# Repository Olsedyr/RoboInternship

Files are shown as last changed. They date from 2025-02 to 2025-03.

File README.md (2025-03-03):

# RoboInternship
The github repo for RoboStacker/MPN internship

CompanyDocumentation indeholder dokumentation for firmaets opbygning og kode. 

Brugen af el-dokumenter:

Åben CaddyDFX filerne i et program der understøtter .dfx filtyper, såsom LibreCAD (Open Source)

DFXComponentsLibrary består af komponenter i .dfx formatet. 

Eksempel til implementering a DFXComponentsLibrary i LibreCAD:

	1. Åben LibreCad
	2. Klik på 'options' 
	3. Vælg 'Apllication Preferences' 
	4. Gå til 'Paths'	
	5. Indsæt stien til DFXComponentsLibrary fra GitHub-repo klonen i 'part libraries' feltet. 
	6. Genstart libreCAD

 For at tilføje flere komponenter skal mappen med de nye komponenter i filformatet .dfx indsættet i DFXComponentsLibrary-mappen.

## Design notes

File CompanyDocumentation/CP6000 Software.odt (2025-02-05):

CP6000 v2007 software

Preliminary Technical Manual

# Statemashines

## Standard Statemachines

### 708WorkCell.statemachine

File containing other file names, which should be included in the workcell.

STATEMACHINEVERSION 3

Include=cpworkcell.statemachine

Link=PIDBuffer ServoBuffer

Link=PIDLift ServoLift

Link=PIDSkub ServoSkub

Link=extra1 AccumulatingConveyor

(Inlcude cpworkcell.statemachine below:)

STATEMACHINEVERSION 3

Name=WorkCell

Link=Emergency

Link=ContinueKnap

Link=ErrorCode

Link=BufferPlads

Link=KasseInLiner

Link=KasseLift

Link=LangBufferSkub

Link=PIDBuffer

Link=PIDLift

Link=PIDSkub

Link=ProductConveyors

Link=extra1 ProductConveyors

linkValue=newprogram Program

Value=errorCode 0

Value=firstRun 0

Value=doFakeProducts 0

Timeout=timeBeforeRunning 3000000

Timeout=timeBeforePausing 2000000

State=ST_HALT

END

State=ST_IDLE

SET errorCode 0

TEST ContinueKnap = ST_HIGH

TIMEOUT timeBeforeRunning ST_STARTING

SETSTATE ST_STARTING

ENDTEST

END

State=ST_STARTING

SET firstRun 1

TEST timeBeforeRunning = 1

SETSTATE ST_RUNNING

ENDTEST

TEST Emergency = ST_POWEROFF

SET errorCode 203

SETSTATE ST_ERROR

ENDTEST

END

State=ST_RESTARTING

SET firstRun 0

TEST timeBeforeRunning = 1

SETSTATE ST_RUNNING

ENDTEST

TEST Emergency = ST_POWEROFF

SET errorCode 203

SETSTATE ST_ERROR

ENDTEST

END

State=ST_RUNNING

TEST ContinueKnap = ST_HIGH

TIMEOUT timeBeforePausing ST_PAUSING

SETSTATE ST_PAUSING

ENDTEST

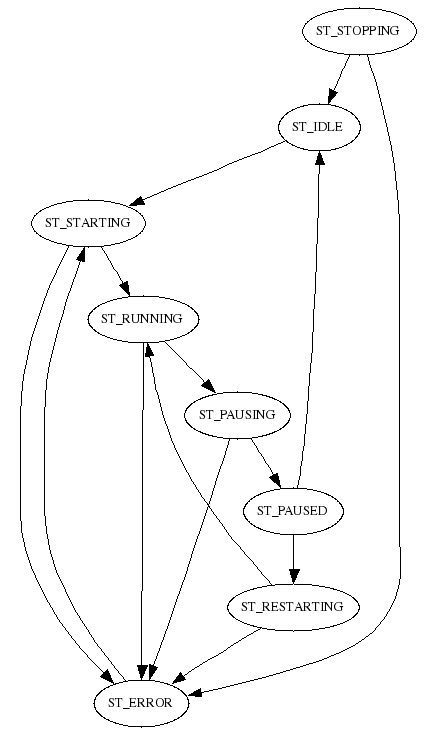
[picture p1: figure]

Fig 1: 708Workcell.statemachine

TEST ErrorCode = ST_ERROR

TIMEOUT timeBeforePausing ST_PAUSING

SETSTATE ST_PAUSING

ENDTEST

TEST Emergency = ST_POWEROFF

SET errorCode 203

SETSTATE ST_ERROR

ENDTEST

END

State=ST_STOPPING

SETSTATE ST_IDLE

TEST Emergency = ST_POWEROFF

SET errorCode 203

SETSTATE ST_ERROR

ENDTEST

END

State=ST_PAUSING

; dont test for trafficlight :-)

TEST timeBeforePausing = 1

AND BufferPlads = ST_IDLE

AND KasseInLiner = ST_IDLE

AND KasseLift = ST_IDLE

AND LangBufferSkub = ST_IDLE

AND PIDBuffer = ST_IDLE

AND PIDLift = ST_IDLE

AND PIDSkub = ST_IDLE

AND ProductConveyors = ST_IDLE

AND extra1 = ST_IDLE

SETSTATE ST_PAUSED

ENDTEST

TEST Emergency = ST_POWEROFF

SET errorCode 203

SETSTATE ST_ERROR

ENDTEST

END

State=ST_PAUSED

TEST newprogram = 1

SETSTATE ST_IDLE

ELSE

TEST ContinueKnap = ST_HIGH

SET firstRun 0

TIMEOUT timeBeforeRunning ST_RESTARTING

SETSTATE ST_RESTARTING

ENDTEST

ENDTEST

END

State=ST_ERROR

TEST ContinueKnap = ST_HIGH

SET errorCode 0

TIMEOUT timeBeforeRunning ST_STARTING

SETSTATE ST_STARTING

ENDTEST

END

State=ST_RESET

END

State=ST_TIMER

END

### 708Parent.statemachine

STATEMACHINEVERSION 3

Name=Parent

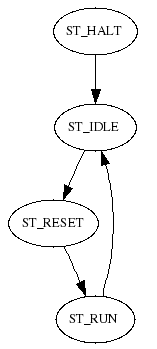
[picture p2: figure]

Fig 2: 708Parent.statemachine

Link=WorkCell WorkCell

State=ST_HALT

SETSTATE ST_IDLE

END

State=ST_TIMER

END

State=ST_IDLE

TEST WorkCell = ST_STARTING

OR WorkCell = ST_RESTARTING

SETSTATE ST_RESET

ENDTEST

END

State=ST_RUN

TEST WorkCell = ST_IDLE

OR WorkCell = ST_PAUSED

OR WorkCell = ST_PAUSING

OR WorkCell = ST_ERROR

SETSTATE ST_IDLE

ENDTEST

END

State=ST_RESET

SETSTATE ST_RUN

END

### 708Program.statemachine

Example program:

STATEMACHINEVERSION 3

Name=Program

Link=workcell WorkCell

Value=usersection 0

Const=programidx 1

Value=loadfromleft 0

Value=loadfromright 0

Value=productsfromleft 0

Value=productsfromright 0

Value=newprogram 1

Value=timeMotorInGoDown 0

Value=timeKlapDown 0

Value=noShakeOnLast 0

Value=waitInR3 0

Value=vibrateTime 8000000

Value=manuelt 0

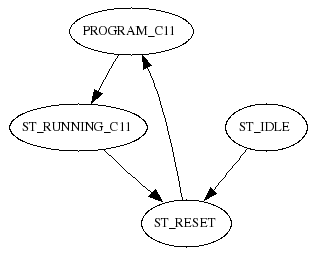
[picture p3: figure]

fig 3: 708Program.statemachine

Value=kasseStopType 1

Value=secondProdConvOn 0

;programmer

Value=program 0

Item=item C11

Item=itemC11 C11

CPPattern=cppHarndrup Harndrup

State=PROGRAM_C11

SET usersection 0

SET newprogram 1

SET loadfromleft 1

SET loadfromright 0

SET productsfromleft 0

SET productsfromright 1

SET secondProdConvOn 0

SET program 0

SET manuelt 0

SET usersection 1 ; user editable below

;

SETITEM item itemC11

SETCPPATTERN cppattern cppHarndrup

SET timeMotorInGoDown 0

SET timeKlapDown 300000

SET noShakeOnLast 0

SET waitInR3 0

SET vibrateTime 800000

SETSTATE ST_RUNNING_C11

END

State=ST_RUNNING_C11

SET newprogram 0

TEST workcell = ST_IDLE

OR workcell = ST_PAUSED

TEST programidx != program

SETSTATE ST_RESET

ENDTEST

ENDTEST

END

State=ST_TIMER

END

State=ST_HALT

END

State=ST_IDLE

SETSTATE ST_RESET

END

State=ST_RESET

TEST programidx = 0

SETSTATE PROGRAM_C11

ENDTEST

END

### 708ErrorCode.statemachine

STATEMACHINEVERSION 3

Include=cperrorcode.statemachine

Name=ErrorCode

linkValue=pidbuffer errorCode ServoBuffer

linkValue=pidlift errorCode ServoLift

linkValue=pidskub errorCode ServoSkub

linkValue=remotewatch errorCode IOError

STATEMACHINEVERSION 3

Name=ErrorCode

Link=parent Parent

linkValue=workcell errorCode WorkCell

linkValue=emergency errorCode Emergency

linkValue=tripwatch errorCode TripWatch

linkValue=pidbuffer errorCode PIDBuffer

linkValue=pidlift errorCode PIDLift

linkValue=pidskub errorCode PIDSkub

linkValue=langbufferskub errorCode LangBufferSkub

linkValue=remotewatch errorCode RemoteWatch

linkValue=kasseinliner errorCode KasseInLiner

linkValue=kasselift errorCode KasseLift

linkValue=productcount errorCode ProductCount

linkValue=ioerror errorCode IOError

State=ST_HALT

END

State=ST_TIMER

END

State=ST_IDLE

TEST parent = ST_RESET

SETSTATE ST_RESET

ENDTEST

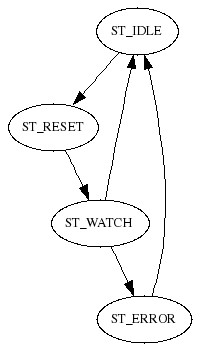
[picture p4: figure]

fig 4: 708ErrorCode.statemachine

END

State=ST_RESET

SETSTATE ST_WATCH

END

State=ST_WATCH

TEST workcell != 0

OR emergency != 0

OR tripwatch != 0

OR pidbuffer != 0

OR pidlift != 0

OR pidskub != 0

OR langbufferskub != 0

OR remotewatch != 0

OR kasseinliner != 0

OR kasselift != 0

OR productcount != 0

OR ioerror != 0

SETSTATE ST_ERROR

ENDTEST

TEST parent = ST_IDLE

SETSTATE ST_IDLE

ENDTEST

END

State=ST_ERROR

TEST parent = ST_IDLE

SETSTATE ST_IDLE

ENDTEST

END

### 708ContinueKnap.statemachine

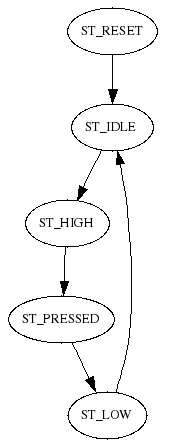
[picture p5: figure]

fig 5:708ContinueKnap.statemachine

STATEMACHINEVERSION 3

Include=continueknap.statemachine

Name=ContinueKnap

Input=Knap ""

Timeout=TimeoutDelay 2000000

STATEMACHINEVERSION 3

Name=ContinueKnap

Input=Knap "dummyOff"

Const=useKnap 1

Value=knap 0

Timeout=TimeoutDelay 2000000

Timeout=startDelay 0

State=ST_HALT

END

State=ST_TIMER

END

State=ST_IDLE

TEST knap = 1

TIMEOUT startDelay ST_HIGH

SETSTATE ST_TIMER

ELSE

TEST Knap = 1

AND useKnap = 1

TIMEOUT startDelay ST_HIGH

SETSTATE ST_TIMER

ENDTEST

ENDTEST

END

State=ST_HIGH

TIMEOUT TimeoutDelay ST_PRESSED

SETSTATE ST_PRESSED

END

State=ST_PRESSED

TEST TimeoutDelay = 1

SETSTATE ST_LOW

ENDTEST

END

State=ST_LOW

SET knap 0

SETSTATE ST_IDLE

END

State=ST_RESET

SETSTATE ST_IDLE

END

### 708TrafficLight.statemachine

STATEMACHINEVERSION 3

Include=trafficlight.statemachine

Name=TrafficLight

Output=green "Green Light"

Output=yellow "Yellow Light"

Output=red "dummyOut"

Timeout=blinkRate 500000

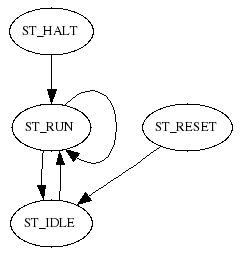
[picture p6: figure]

fig 6: 708TrafficLight.statemachine

Link=workcell WorkCell

Link=emergency Emergency

Value=OFF 0

Value=ON 1

Value=BLINK 0

STATEMACHINEVERSION 3

Name=TrafficLight

Output=green "Green Light"

Output=yellow "Yellow Light"

Output=red "dummyOut"

Timeout=blinkRate 500000

Link=workcell WorkCell

Link=emergency Emergency

Link=errorcode ErrorCode

Value=OFF 0

Value=ON 1

Value=BLINK 0

Value=error 0

Const=enable 1

State=ST_HALT

TIMEOUT blinkRate ST_RUN

SETSTATE ST_RUN

END

State=ST_TIMER

END

State=ST_IDLE

TEST enable = 1

TIMEOUT blinkRate ST_RUN

SETSTATE ST_RUN

ENDTEST

END

State=ST_RESET

SET error 0

SETSTATE ST_IDLE

END

State=ST_RUN

TEST enable = 0

SETSTATE ST_IDLE

ENDTEST

TEST errorcode = ST_ERROR

SET error 1

ENDTEST

TEST blinkRate = 1

TEST BLINK = ON

SET BLINK OFF

ELSE

SET BLINK ON

ENDTEST

TIMEOUT blinkRate ST_RUN

SETSTATE ST_RUN

ENDTEST

TEST emergency = ST_POWEROFF

SET red ON

SET yellow OFF

SET green OFF

ELSE

TEST workcell = ST_IDLE

SET error 0

SET red OFF

SET yellow ON

SET green OFF

ELSE

TEST workcell = ST_STARTING

OR workcell = ST_RESTARTING

OR workcell = ST_PAUSING

SET red OFF

SET yellow ON

SET green BLINK

ELSE

TEST workcell = ST_RUNNING

SET error 0

SET red OFF

SET yellow OFF

SET green ON

ELSE

TEST workcell = ST_PAUSED

SET red OFF

TEST error = 0

SET yellow BLINK

SET green BLINK

ELSE

SET yellow BLINK

SET green OFF

ENDTEST

ELSE

TEST workcell = ST_ERROR

SET red OFF

SET yellow BLINK

SET green OFF

ELSE

SET red BLINK

SET yellow OFF

SET green OFF

ENDTEST

ENDTEST

ENDTEST

ENDTEST

ENDTEST

ENDTEST

END

### 708Emergency.statemachine

STATEMACHINEVERSION 3

Include=cpemergency.statemachine

Name=Emergency

Input=EmergencyOK "Emergency OK"

Output=PowerOK "Styrespaending OK"

STATEMACHINEVERSION 3

Name=Emergency

Input=EmergencyOK "dummyOn"

Output=PowerOK "dummyOut"

Value=errorCode 0

Const=errorCode101 101

Timeout=delayOn 1000000

Value=simulate 0

State=ST_TIMER

END

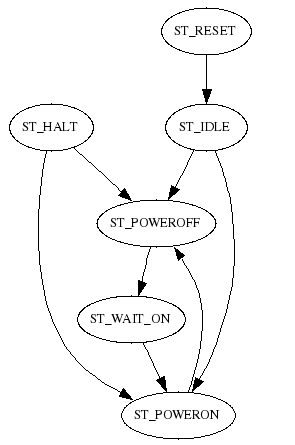
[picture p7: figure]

fig 7: 708Emergency.statemachine

State=ST_HALT

TEST EmergencyOK = 0

AND simulate = 0

SETSTATE ST_POWEROFF

ELSE

SETSTATE ST_POWERON

ENDTEST

END

State=ST_IDLE

TEST EmergencyOK = 0

AND simulate = 0

SETSTATE ST_POWEROFF

ELSE

SETSTATE ST_POWERON

ENDTEST

END

State=ST_POWEROFF

SET errorCode errorCode101

SET PowerOK 0

TEST EmergencyOK = 1

OR simulate = 1

TIMEOUT delayOn ST_WAIT_ON

SETSTATE ST_WAIT_ON

ENDTEST

END

State=ST_WAIT_ON

TEST delayOn = 1

SETSTATE ST_POWERON

ENDTEST

END

State=ST_POWERON

SET errorCode 0

SET PowerOK 1

TEST EmergencyOK = 0

AND simulate = 0

SETSTATE ST_POWEROFF

ENDTEST

END

State=ST_RESET

SETSTATE ST_IDLE

END

### 708IOError.statemachine

STATEMACHINEVERSION 3

Include=ioerror.statemachine

Name=IOError

Link=parent Parent

Value=errorCode 0

Value=advantyserror 0

Value=comskerror 0

Value=trioerror 0

Value=loadcellerror 0

Const=ioerrorcode 500

STATEMACHINEVERSION 3

Name=IOError

Link=parent Parent

Value=errorCode 0

Value=advantyserror 0

Value=comskerror 0

Value=trioerror 0

Value=loadcellerror 0

Value=macerror 0

Value=icpconerror 0

; TODO Implement trio error i drivers

State=ST_HALT

END

State=ST_TIMER

END

State=ST_IDLE

TEST advantyserror != 0

SET errorCode 501

ELSETEST comskerror != 0

SET errorCode 502

ELSETEST trioerror != 0

SET errorCode 503

ELSETEST loadcellerror != 0

SET errorCode 504

ELSETEST macerror != 0

SET errorCode 505

ELSETEST icpconerror != 0

SET errorCode 506

ENDTEST

TEST parent = ST_RESET

SET advantyserror 0

SET comskerror 0

SET trioerror 0

SET loadcellerror 0

SET macerror 0

SET errorCode 0

ENDTEST

END

### 708TripWatch.statemachine

STATEMACHINEVERSION 3

Include=cptripwatch2.statemachine

Name=TripWatch

Input=conveyor2 "ProduktConveyor_2 HZOK"

Input=extra1 "Accumulating Conveyor HZOK"

Const=extra1Pol 0

;** User section **

STATEMACHINEVERSION 3

Name=TripWatch

Input=conveyor1 "ProduktConveyor_1 HZOK"

Input=conveyor2 "dummyOn"

Input=skubberstatus "LangBufferSkub Status"

Input=bufferstatus "BufferPlads Status"

Input=liftstatus "KasseLift Status"

Input=inliner "KasseInliner Motor Tripped"

Input=liftconveyor "KasseLift Conveyor Motor Tripped"

Input=vibrator "KasseLift Vibrator Tripped"

Input=extra1 "dummyOff"

Const=extra1Pol 1

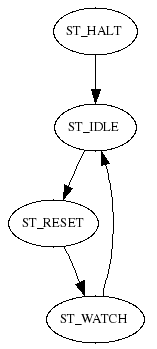
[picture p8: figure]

fig 8: 708TripWatch.statemachine

Const=extra1ErrorCode 1100

Link=parent Parent

Value=errorCode 0

State=ST_TIMER

END

State=ST_HALT

SETSTATE ST_IDLE

END

State=ST_IDLE

TEST parent = ST_RESET

SET errorCode 0

SETSTATE ST_RESET

ENDTEST

END

State=ST_RESET

SETSTATE ST_WATCH

END

State=ST_WATCH

TEST conveyor1 = 0

OR conveyor2 = 0

SET errorCode 1100

ENDTEST

TEST skubberstatus != 16

AND skubberstatus != 32

AND skubberstatus != 48

AND skubberstatus != 64

AND skubberstatus != 80

AND skubberstatus != 0

SET errorCode 1101

ENDTEST

TEST bufferstatus != 16

AND bufferstatus != 32

AND bufferstatus != 48

AND bufferstatus != 64

AND bufferstatus != 80

AND bufferstatus != 0

SET errorCode 1102

ENDTEST

TEST liftstatus != 16

AND liftstatus != 32

AND liftstatus != 48

AND liftstatus != 64

AND liftstatus != 80

AND liftstatus != 0

SET errorCode 1103

ENDTEST

TEST inliner = 1

SET errorCode 1104

ENDTEST

TEST liftconveyor = 1

SET errorCode 1105

ENDTEST

TEST vibrator = 1

SET errorCode 1106

ENDTEST

TEST extra1 = extra1Pol

SET errorCode extra1ErrorCode

ENDTEST

TEST parent = ST_IDLE

SETSTATE ST_IDLE

ENDTEST

END

## Product Handling Statemachines

### 708ProductConveyors.statemachine

STATEMACHINEVERSION 3

Include=cpproductconveyors.statemachine

Name=ProductConveyors

Input=powerok1 "ProduktConveyor_1 HZOK"

Input=powerok2 "ProduktConveyor_2 HZOK"

Output=Motor1Enable "ProductConveyor1 Motor Enable"

Output=Motor1Setpoint "ProductConveyor1 Setpoint"

Output=Motor2Enable "ProductConveyor2 Motor Enable"

Output=Motor2Setpoint "ProductConveyor2 Setpoint"

Link=CamGenSkub ServoSkub

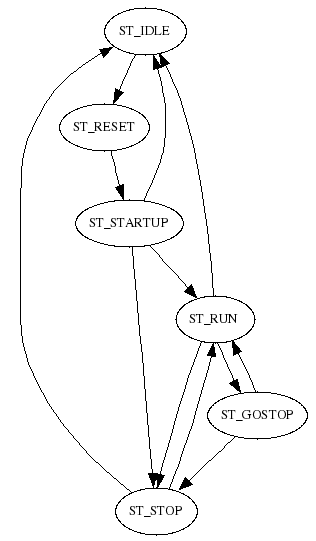
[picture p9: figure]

fig 9: 708ProductConveyors.statemachine

Const=motor1FreqForward -40.0000

Const=motor1FreqReverse 40.0000

Const=motor2FreqForward -45.0000

Const=motor2FreqReverse 45.0000

Timeout=TimeRunAgain 100000

;** User section **

STATEMACHINEVERSION 3

Name=ProductConveyors

Input=powerok1 "dummyOff"

Input=powerok2 "dummyOff"

Output=Motor1Enable "dummyOut"

Output=Motor1Setpoint "dummyOut"

Output=Motor2Enable "dummyOut"

Output=Motor2Setpoint "dummyOut"

Link=Counter ProductCount

Link=CamGenSkub

Link=parent LangBufferSkub

linkValue=prenumofproducts Counter

linkValue=oldppp Counter

linkValue=productsfromleft Program

linkValue=productsfromright Program

Value=ppp 0

linkValue=secondProdConvOn Program

Const=motor1FreqForward 50.0

Const=motor1FreqReverse -50.0

Const=motor2FreqForward 50.0

Const=motor2FreqReverse -50.0

Timeout=TimeStop 0

Timeout=TimeRunAgain 600000

Input=syncInManuelStop "dummyOff"

Const=useSyncInManuelStop 0

Const=syncInManuelStopPol 1

State=ST_TIMER

END

State=ST_HALT

END

State=ST_IDLE

SET Motor1Enable 0

SET Motor1Setpoint 0.0

SET Motor2Enable 0

SET Motor2Setpoint 0.0

TEST parent = ST_RESET

SETSTATE ST_RESET

ENDTEST

END

State=ST_RESET

SET Motor1Enable 1

SET Motor2Enable 1

SETSTATE ST_STARTUP

END

State=ST_STARTUP

TEST Counter = ST_RUN

OR Counter = ST_RUN_MANUELT

CALC ppp = oldppp + 1

TEST prenumofproducts >= ppp

SETSTATE ST_STOP

ELSE

TEST useSyncInManuelStop = 1

AND syncInManuelStop = syncInManuelStopPol

AND Counter = ST_RUN_MANUELT

SETSTATE ST_STOP

ELSE

TEST CamGenSkub != ST_NOCHOOSETRACK

SETSTATE ST_RUN

ENDTEST

ENDTEST

ENDTEST

ENDTEST

TEST parent = ST_IDLE

SETSTATE ST_IDLE

ENDTEST

END

State=ST_RUN

TEST useSyncInManuelStop = 1

AND syncInManuelStop = syncInManuelStopPol

AND Counter = ST_RUN_MANUELT

SETSTATE ST_STOP

ELSE

CALC ppp = oldppp + 1

TEST prenumofproducts >= ppp

TIMEOUT TimeStop ST_GOSTOP

SETSTATE ST_GOSTOP

ELSE

TEST productsfromleft = 1

AND productsfromright = 1

SET Motor1Enable 1

SET Motor1Setpoint motor1FreqForward

SET Motor2Enable 1

SET Motor2Setpoint motor2FreqForward

ELSE

TEST productsfromleft = 1

TEST secondProdConvOn = 1

SET Motor1Enable 1

SET Motor1Setpoint motor1FreqForward

SET Motor2Enable 1

SET Motor2Setpoint motor2FreqReverse

ELSE

SET Motor1Enable 1

SET Motor1Setpoint motor1FreqForward

SET Motor2Enable 0

SET Motor2Setpoint 0.0

ENDTEST

ELSE

TEST productsfromright = 1

TEST secondProdConvOn = 1

SET Motor1Enable 1

SET Motor1Setpoint motor1FreqReverse

SET Motor2Enable 1

SET Motor2Setpoint motor2FreqForward

ELSE

SET Motor1Enable 0

SET Motor1Setpoint 0.0

SET Motor2Enable 1

SET Motor2Setpoint motor2FreqForward

ENDTEST

ENDTEST

ENDTEST

ENDTEST

ENDTEST

ENDTEST

TEST powerok1 = 0

OR powerok2 = 0

SETSTATE ST_IDLE

ENDTEST

TEST parent = ST_IDLE

SETSTATE ST_IDLE

ENDTEST

END

State=ST_GOSTOP

CALC ppp = oldppp + 1

TEST TimeStop = 1

SETSTATE ST_STOP

ENDTEST

TEST prenumofproducts < ppp

SETSTATE ST_RUN

ENDTEST

END

State=ST_STOP

CALC ppp = oldppp + 1

TEST useSyncInManuelStop = 1

AND syncInManuelStop = syncInManuelStopPol

AND Counter = ST_RUN_MANUELT

SET Motor1Enable 0

SET Motor1Setpoint 0.0

SET Motor2Enable 0

SET Motor2Setpoint 0.0

ELSE

TEST prenumofproducts >= ppp

SET Motor1Enable 0

SET Motor1Setpoint 0.0

SET Motor2Enable 0

SET Motor2Setpoint 0.0

ELSE

TIMEOUT TimeRunAgain ST_RUN

SETSTATE ST_TIMER

ENDTEST

ENDTEST

TEST parent = ST_IDLE

SETSTATE ST_IDLE

ENDTEST

END

### 708Product1Foto1.statemachine

STATEMACHINEVERSION 3

Include=input.statemachine

Name=Product1Foto1

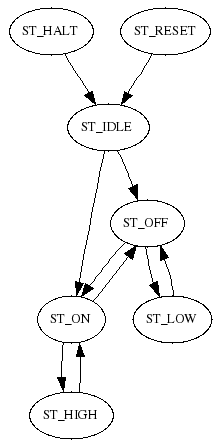
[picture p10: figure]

fig 10: input.statemachine

Input=input "ProduktConveyor1 Foto1"

Timeout=TimeOn 10000

Timeout=TimeOff 50000

Value=test 0

Link=parent Parent

STATEMACHINEVERSION 3

Name=Input

Input=input "dummyOff"

;how long must input be active before it is recognised as on

Timeout=TimeOn 1000000

;how long must input be not active before it is recognised as off

Timeout=TimeOff 1000000

Value=test 0

Const=active 1

State=ST_HALT

SETSTATE ST_IDLE

END

State=ST_TIMER

END

State=ST_RESET

SETSTATE ST_IDLE

END

State=ST_IDLE

TEST input != active

SET test 0

TIMEOUT TimeOff ST_OFF

SETSTATE ST_OFF

ELSE

SET test 1

TIMEOUT TimeOn ST_ON

SETSTATE ST_ON

ENDTEST

END

State=ST_OFF

TEST input = active

TIMEOUT TimeOn ST_ON

SETSTATE ST_ON

ELSE

TEST TimeOff = 1

AND test = 1

SETSTATE ST_LOW

ENDTEST

ENDTEST

END

State=ST_ON

TEST input != active

TIMEOUT TimeOff ST_OFF

SETSTATE ST_OFF

ELSE

TEST TimeOn = 1

AND test = 0

SETSTATE ST_HIGH

ENDTEST

ENDTEST

END

State=ST_LOW

SET test 0

SETSTATE ST_OFF

END

State=ST_HIGH

SET test 1

SETSTATE ST_ON

END

### 708Product1Foto2.statemachine

STATEMACHINEVERSION 3

Include=input.statemachine

Name=Product1Foto2

Input=input "ProduktConveyor1 Foto2"

Timeout=TimeOn 100000

Timeout=TimeOff 10000

Value=test 0

Link=parent Parent

### 708Product2Foto1.statemachine

STATEMACHINEVERSION 3

Include=input.statemachine

Name=Product2Foto1

Input=input "ProduktConveyor2 Foto1"

Timeout=TimeOn 100000

Timeout=TimeOff 100000

Value=test 0

Link=parent Parent

### 708Product2Foto2.statemachine

STATEMACHINEVERSION 3

Include=input.statemachine

Name=Product2Foto2

Input=input "ProduktConveyor2 Foto2"

Timeout=TimeOn 100000

Timeout=TimeOff 100000

Value=test 0

Link=parent Parent

### 708AccumulatingConveyorQueFullFoto.statemachine

STATEMACHINEVERSION 3

Include=input.statemachine

Name=AccumulatingConveyorQueFullFoto

Input=input "Accumulating Conveyor Que Full Foto"

Timeout=TimeOn 50000

Timeout=TimeOff 50000

Value=test 0

Link=parent Parent

### 708AccumulatingConveyor.statemachine

STATEMACHINEVERSION 3

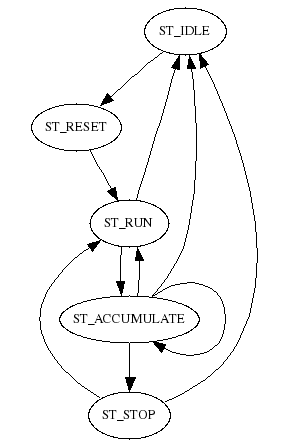
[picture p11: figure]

fig 11: 708AccumulatingConveyor.statemachine

Name=AccumulatingConveyor

;** Input **

Input=powerok "Accumulating Conveyor HZOK"

;** Output **

Output=motorEnable "Accumulating Conveyor Enable"

Output=motor "Accumulating Conveyor Setpoint"

Output=clap "Accumulating Conveyor Clap"

Output=startulma "Sync Out 1"

;** Link **

Link=queFoto AccumulatingConveyorQueFullFoto

Link=master ProductConveyors

;** linkValue **

;** Const **

Const=motorSpeed 45.0000

;** Value **

Value=queFotoOn 0

;** Timeout **

Timeout=queFullStopTime 1000000

State=ST_HALT

END

State=ST_TIMER

END

State=ST_IDLE

SET motorEnable 0

SET startulma 0

SET motor 0.0

TEST master = ST_RUN

SETSTATE ST_RESET

ENDTEST

END

State=ST_RESET

SETSTATE ST_RUN

END

State=ST_RUN

TEST master = ST_RUN

SET motorEnable 1

SET startulma 1

SET motor motorSpeed

SET clap 0

ELSE

SETSTATE ST_ACCUMULATE

ENDTEST

TEST master = ST_IDLE

OR powerok = 0

SETSTATE ST_IDLE

ENDTEST

END

State=ST_ACCUMULATE

TEST master = ST_RUN

SETSTATE ST_RUN

ELSE

SET clap 1

TEST queFoto = ST_ON

TEST queFotoOn = 0

SET queFotoOn 1

TIMEOUT queFullStopTime ST_ACCUMULATE

SETSTATE ST_ACCUMULATE

ELSE

TEST queFullStopTime = 1

SET queFotoOn 0

SETSTATE ST_STOP

ENDTEST

ENDTEST

ELSE

SET queFotoOn 0

ENDTEST

ENDTEST

TEST master = ST_IDLE

OR powerok = 0

SET queFotoOn 0

SETSTATE ST_IDLE

ENDTEST

END

State=ST_STOP

TEST master = ST_RUN

SETSTATE ST_RUN

ELSE

SET motorEnable 0

SET startulma 0

SET motor 0.0

SET clap 1

ENDTEST

TEST master = ST_IDLE

OR powerok = 0

SETSTATE ST_IDLE

ENDTEST

END

### 708CPCounter.statemachine

STATEMACHINEVERSION 3

Include=cpcounter.statemachine

Name=CPCounter

STATEMACHINEVERSION 3

Name=CPCounter

Link=foto1 Product1Foto1

Link=foto2 Product2Foto1

Link=parent Parent

linkValue=firstRun WorkCell

linkValue=productsfromleft Program

linkValue=productsfromright Program

Table=avgtime 20.0 AVG

Value=curt 0

Value=temp 0.0

Value=temp2 0.0

Value=now 0.0

Value=avg 0.0

Value=avgtimetol 0.0

Value=prodpermin 0.0

Timeout=MinTime 30000000

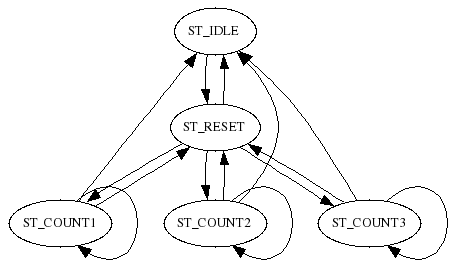
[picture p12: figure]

fig 12: 708CPCounter.statemachine

State=ST_HALT

END

State=ST_TIMER

END

State=ST_IDLE

TEST parent = ST_RESET

SETSTATE ST_RESET

ENDTEST

END

State=ST_RESET

SET avgtime 600.0

SET avgtime 600.0

SET avgtime 600.0

SET avgtime 600.0

SET avgtime 600.0

SET avgtime 600.0

SET avgtime 600.0

SET avgtime 600.0

SET avgtime 600.0

SET avgtime 600.0

SET avgtime 600.0

SET avgtime 600.0

SET avgtime 600.0

SET avgtime 600.0

SET avgtime 600.0

SET avgtime 600.0

SET avgtime 600.0

SET avgtime 600.0

SET avgtime 600.0

SET avgtime 600.0

SET avg 600.0

SET prodpermin 0.0

TEST productsfromleft = 1

AND productsfromright = 1

TIMEOUT MinTime ST_COUNT1

SETSTATE ST_COUNT1

ELSE

TEST productsfromleft = 1

TIMEOUT MinTime ST_COUNT2

SETSTATE ST_COUNT2

ELSE

TEST productsfromright = 1

TIMEOUT MinTime ST_COUNT3

SETSTATE ST_COUNT3

ELSE

SETSTATE ST_IDLE

ENDTEST

ENDTEST

ENDTEST

END

State=ST_COUNT1

SET curt MinTime

CALC curt = MinTime - curt

CALC now = curt / 1000000.0

TEST foto1 = ST_LOW

AND foto2 = ST_LOW

TIMEOUT MinTime ST_COUNT1

SETSTATE ST_COUNT1

SET avgtime now

SET avgtime now

SET avg avgtime

ELSE

TEST foto1 = ST_LOW

TIMEOUT MinTime ST_COUNT1

SETSTATE ST_COUNT1

SET avgtime now

SET avg avgtime

ELSE

TEST foto2 = ST_LOW

TIMEOUT MinTime ST_COUNT1

SETSTATE ST_COUNT1

SET avgtime now

SET avg avgtime

ELSE

TEST MinTime = 1

SET avg 600.0

SETSTATE ST_RESET

ELSE

SET avg avgtime

ENDTEST

ENDTEST

ENDTEST

ENDTEST

CALC prodpermin = 60.0 / avg

TEST parent = ST_IDLE

SETSTATE ST_IDLE

ENDTEST

END

State=ST_COUNT2

SET curt MinTime

CALC curt = MinTime - curt

CALC now = curt / 1000000.0

TEST foto1 = ST_LOW

TIMEOUT MinTime ST_COUNT2

SETSTATE ST_COUNT2

SET avgtime now

SET avg avgtime

ELSE

TEST MinTime = 1

SET avg 600.0

SETSTATE ST_RESET

ELSE

SET avg avgtime

ENDTEST

ENDTEST

CALC prodpermin = 60.0 / avg

TEST parent = ST_IDLE

SETSTATE ST_IDLE

ENDTEST

END

State=ST_COUNT3

SET curt MinTime

CALC curt = MinTime - curt

CALC now = curt / 1000000.0

TEST foto2 = ST_LOW

TIMEOUT MinTime ST_COUNT3

SETSTATE ST_COUNT3

SET avgtime now

SET avg avgtime

ELSE

TEST MinTime = 1

SET avg 600.0

SETSTATE ST_RESET

ELSE

SET avg avgtime

ENDTEST

ENDTEST

CALC prodpermin = 60.0 / avg

TEST parent = ST_IDLE

SETSTATE ST_IDLE

ENDTEST

END

### 708ProductCount.statemachine

STATEMACHINEVERSION 3

Include=cpproductcount.statemachine

Name=ProductCount

Link=CamGenSkub ServoSkub

Link=rfoto1 Product1Foto1

Link=rfoto2 Product1Foto2

Link=lfoto1 Product2Foto1

Link=lfoto2 Product2Foto2

;** User section **

Value=superhack_AdjustProdConv1Foto2AndEdit708ProductCount

Value=rfoto2test 1

State=ST_IDLE

TEST parent = ST_RESET

PRINT superhack_AdjustProdConv1Foto2AndEdit708ProductCount

SETSTATE ST_RESET

ENDTEST

END

STATEMACHINEVERSION 3

Name=ProductCount

;** Input **

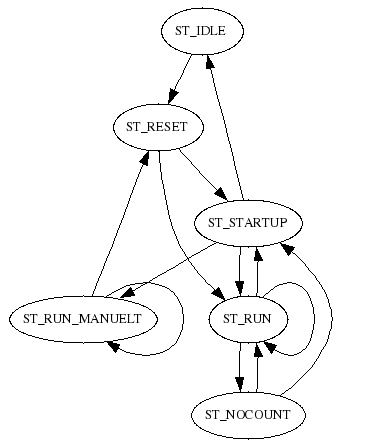
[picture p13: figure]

fig 13: 708ProductCount.statemachine

;** Output **

;** Link **

Link=Skubber LangBufferSkub

Link=CamGenSkub

Link=parent Parent

Link=KasseLift

Link=lfoto1 Product1Foto1

Link=lfoto2 Product1Foto2

Link=rfoto1 Product2Foto1

Link=rfoto2 Product2Foto2

Link=PushPattern

Link=Conveyors ProductConveyors

;** linkValue **

linkValue=lfoto1test test lfoto1

linkValue=lfoto2test test lfoto2

linkValue=rfoto1test test rfoto1

linkValue=rfoto2test test rfoto2

linkValue=curpm CamGenSkub

linkValue=curppp PushPattern

linkValue=productsfromleft Program

linkValue=productsfromright Program

linkValue=firstRun WorkCell

linkValue=manuelt Program

linkValue=doFakeProducts WorkCell

;** Table **

;** Item **

;** Const **

Const=freepmstay 350

Const=freepmforward 200

;** Value **

Value=errorCode 0

Value=message 0

Value=numofproducts 0

Value=prenumofproducts 0

Value=totcount 0

Value=lowcount 0

Value=pushtotcount 0

Value=pushing 0

Value=oldppp 0

Value=timeStopOn 0

;** Timeout **

Timeout=fakeProductRate 2000000

Timeout=TimeStartUp 1500000

Timeout=maxProductLengthStopTime 2000000

Timeout=TimeStop 1000000

State=ST_TIMER

END

State=ST_HALT

END

State=ST_IDLE

TEST parent = ST_RESET

SETSTATE ST_RESET

ENDTEST

END

State=ST_RESET

SET errorCode 0

SET numofproducts 0

SET totcount 0

SET lowcount 0

SET pushtotcount 0

TEST firstRun = 1

TIMEOUT TimeStartUp ST_STARTUP

SETSTATE ST_STARTUP

ELSE

TIMEOUT fakeProductRate ST_RUN

SETSTATE ST_RUN

ENDTEST

END

State=ST_STARTUP

SET oldppp curppp

TEST TimeStartUp = 1

TIMEOUT fakeProductRate ST_RUN

SETSTATE ST_RUN

TEST productsfromleft = 1

AND productsfromright = 1

TEST lfoto1test = 0

OR lfoto2test = 0

OR rfoto1test = 0

OR rfoto2test = 0

SET errorCode 1055

SETSTATE ST_IDLE

ENDTEST

SET numofproducts 0

SET totcount 0

SET pushtotcount 0

SET prenumofproducts numofproducts

ELSE

TEST productsfromleft = 1

TEST lfoto1test = 0

OR lfoto2test = 0

SET errorCode 1055

SETSTATE ST_IDLE

ENDTEST

SET numofproducts 0

SET totcount 0

SET pushtotcount 0

SET prenumofproducts numofproducts

ELSE

TEST productsfromright = 1

TEST rfoto1test = 0

OR rfoto2test = 0

SET errorCode 1055

SETSTATE ST_IDLE

ENDTEST

SET numofproducts 0

SET totcount 0

SET pushtotcount 0

SET prenumofproducts numofproducts

ENDTEST

ENDTEST

ENDTEST

TEST manuelt = 1

SET errorCode 0

SETSTATE ST_RUN_MANUELT

ENDTEST

ENDTEST

END

State=ST_RUN

TEST lfoto1 = ST_HIGH

AND productsfromleft = 1

CALC numofproducts = numofproducts + 1

SET prenumofproducts numofproducts

CALC totcount = pushtotcount + numofproducts

CALC lowcount = lowcount + 1

ENDTEST

TEST lfoto1 = ST_LOW

AND productsfromleft = 1

CALC prenumofproducts = numofproducts + 1

ENDTEST

TEST rfoto1 = ST_HIGH

AND productsfromright = 1

CALC numofproducts = numofproducts + 1

SET prenumofproducts numofproducts

CALC totcount = pushtotcount + numofproducts

CALC lowcount = lowcount + 1

ENDTEST

TEST rfoto1 = ST_LOW

AND productsfromright = 1

CALC prenumofproducts = numofproducts + 1

ENDTEST

TEST pushing = 0

TEST Skubber = ST_FORWARD

TEST curpm > freepmforward

CALC numofproducts = numofproducts - oldppp

CALC prenumofproducts = prenumofproducts - oldppp

CALC pushtotcount = pushtotcount + oldppp

CALC totcount = pushtotcount + numofproducts

SET oldppp curppp

SET pushing 1

ENDTEST

ELSE

TEST Skubber = ST_FORWARDSTAY

TEST curpm > freepmstay

CALC numofproducts = numofproducts - oldppp

CALC prenumofproducts = prenumofproducts - oldppp

CALC pushtotcount = pushtotcount + oldppp

CALC totcount = pushtotcount + numofproducts

SET oldppp curppp

SET pushing 1

ENDTEST

ENDTEST

ENDTEST

ELSE

TEST Skubber != ST_FORWARD

AND Skubber != ST_FORWARDSTAY

AND Skubber != ST_STAY_FINISH

SET pushing 0

ENDTEST

ENDTEST

TEST doFakeProducts = 1

TEST fakeProductRate = 1

CALC numofproducts = numofproducts + 1

SET prenumofproducts numofproducts

CALC totcount = pushtotcount + numofproducts

CALC lowcount = lowcount + 1

TIMEOUT fakeProductRate ST_RUN

SETSTATE ST_RUN

ENDTEST

TEST KasseLift = ST_READY

SET numofproducts 0

SET totcount 0

SET pushtotcount 0

SET prenumofproducts numofproducts

SET doFakeProducts 0

ENDTEST

ENDTEST

TEST firstRun = 1

AND parent = ST_RESET

SET timeStopOn 0

TIMEOUT TimeStartUp ST_STARTUP

SETSTATE ST_STARTUP

ENDTEST

TEST Conveyors = ST_IDLE

TEST timeStopOn = 0

SET timeStopOn 1

TIMEOUT TimeStop ST_RUN

SETSTATE ST_RUN

ELSE

TEST TimeStop = 1

SET timeStopOn 0

SETSTATE ST_NOCOUNT

ENDTEST

ENDTEST

ENDTEST

END

State=ST_NOCOUNT

TEST parent = ST_RESET

TEST firstRun = 1

TIMEOUT TimeStartUp ST_STARTUP

SETSTATE ST_STARTUP

ELSE

SETSTATE ST_RUN

ENDTEST

ENDTEST

END

State=ST_RUN_MANUELT

TEST productsfromright = 1

TEST rfoto1 = ST_OFF

TEST maxProductLengthStopTime = 1

;hack that stops ProductConveyor

SET prenumofproducts 100

SET message 1000

ELSE

SET prenumofproducts 0

SET message 0

ENDTEST

ELSE

TEST rfoto1 = ST_ON

SET prenumofproducts 0

TIMEOUT maxProductLengthStopTime ST_RUN_MANUELT

SETSTATE ST_RUN_MANUELT

ENDTEST

ENDTEST

ELSE

SET prenumofproducts 0

TIMEOUT maxProductLengthStopTime ST_RUN_MANUELT

SETSTATE ST_RUN_MANUELT

ENDTEST

TEST firstRun = 1

AND parent = ST_RESET

SET message 0

SETSTATE ST_RESET

ENDTEST

END

### 708PushPattern.statemachine

STATEMACHINEVERSION 3

Include=cppushpattern2.statemachine

Name=PushPattern

STATEMACHINEVERSION 3

fig 14: 708PushPattern.statemachine

Name=PushPattern

Link=Program

Link=ProductCount

Link=Skubber LangBufferSkub

Link=parent Parent

linkValue=firstRun WorkCell

linkValue=numpush Skubber

linkValue=layers bufferlayers BufferPlads

linkValue=cppattern Program

Value=curppp 0

Value=curpacc 0

Value=curpspeed 0

Value=gettime 350000

Value=maxpush 2

Value=maxlayers 0

;pushshort not supported by cppattern

Value=pushshortleft 0

Value=pushshortright 0

State=ST_TIMER

END

State=ST_HALT

END

State=ST_IDLE

TEST ProductCount = ST_RESET

SETSTATE ST_RESET

ENDTEST

END

State=ST_RESET

SETSTATE ST_GO

END

State=ST_GO

SET maxlayers cppattern.maxlayers

SET cppattern.layeridx layers

SET maxpush cppattern.maxpush

SET gettime cppattern.gettime

SET cppattern.pppidx numpush

SET curppp cppattern.ppp

SET curpacc cppattern.pacc

SET curpspeed cppattern.pspeed

TEST firstRun = 1

AND parent = ST_RESET

SETSTATE ST_RESET

ENDTEST

END

## Servo Statemachines

### 708ServoSkub.statemachine

STATEMACHINEVERSION 3

Include=cpservoskub.statemachine

Name=ServoSkub

;** User section **

Const=cruise_speed 1500.0000

Const=acceleration 3500.0000

STATEMACHINEVERSION 3

Name=ServoSkub

Link=Master LangBufferSkub

Link=parent Parent

Input=homesensor "LangBufferSkub HomeSensor"

Output=Mode "LangBufferSkub Mode"

Output=setpoint "LangBufferSkub MacSetpoint"

Output=vsoll "LangBufferSkub Maxvel"

Output=asoll "LangBufferSkub Maxacc"

Output=set_curpos "LangBufferSkub Curpos"

Output=kvout "LangBufferSkub Load Factor"

Output=set_status "LangBufferSkub Status"

Input=temperature "LangBufferSkub Temperature"

Input=Inpos "LangBufferSkub IN_POS"

Input=curpos "LangBufferSkub Curpos"

Input=curvel "LangBufferSkub Curvel"

Input=status "LangBufferSkub Status"

Value=errorCode 0

Value=curpm 0.0

Const=posBackOffset 2000

Const=posForwardOffset -12000

Const=posRound 240000

Const=loadfactor 1.8000

Value=posRoundHalf 120000

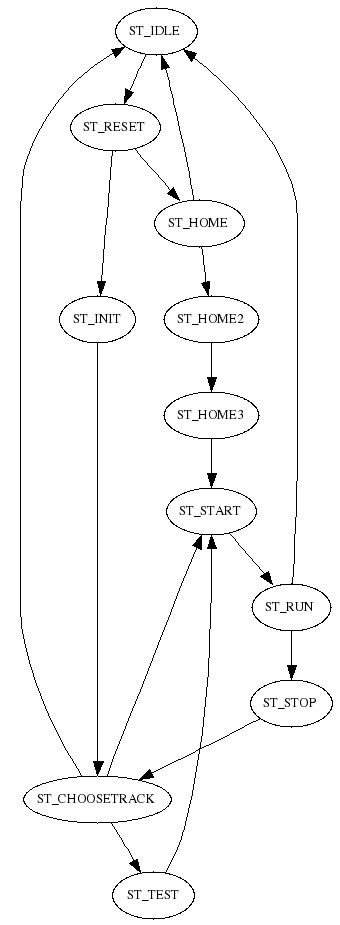
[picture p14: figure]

fig 15: 708ServoSkub.statemachine

Value=homed 0

Value=infwdpos 0

Value=temp 0

Value=ftemp 0.0

Const=homeSensorPol 0

Const=home_speed 300.0000

Const=acceleration 4500.0000

Const=cruise_speed 2750.0000

Const=testmode 0

Value=teststate 0

Value=distance 0.0

Value=startpos 0.0

Timeout=TimeTest 1000000

Timeout=TimeCmdDelay 500000

Timeout=TimeStartMax 1000000

Timeout=TimeHome 10000000

State=ST_TIMER

END

State=ST_HALT

END

State=ST_IDLE

TEST parent = ST_RESET

TEST status != 16

AND status != 32

AND status != 48

AND status != 64

AND status != 80

AND status != 0

SET set_status 0

ENDTEST

SET errorCode 0

SETSTATE ST_RESET

ENDTEST

END

State=ST_RESET

SET kvout loadfactor

CALC posRoundHalf = posRound / 2

SET asoll acceleration

TEST homed = 0

SET vsoll home_speed

SET Mode 1

TIMEOUT TimeHome ST_HOME

SETSTATE ST_HOME

ELSE

SET vsoll cruise_speed

SET setpoint curpos

TIMEOUT TimeCmdDelay ST_INIT

SETSTATE ST_INIT

ENDTEST

END

State=ST_HOME

TEST homesensor = homeSensorPol

SET Mode 0

TIMEOUT TimeCmdDelay ST_HOME2

SETSTATE ST_HOME2

ELSETEST TimeHome = 1

SET errorCode 1050

SET Mode 0

SETSTATE ST_IDLE

ENDTEST

END

State=ST_HOME2

TEST TimeCmdDelay = 1

SET setpoint 0

SET set_curpos 0

SET homed 1

SET Mode 2

TIMEOUT TimeCmdDelay ST_HOME3

SETSTATE ST_HOME3

ENDTEST

END

State=ST_HOME3

TEST TimeCmdDelay = 1

SET vsoll cruise_speed

SET setpoint posBackOffset

SET startpos curpos

SET distance posBackOffset

TIMEOUT TimeStartMax ST_START

SETSTATE ST_START

ENDTEST

END

State=ST_INIT

TEST TimeCmdDelay = 1

SET Mode 2

SETSTATE ST_CHOOSETRACK

ENDTEST

END

State=ST_NOCHOOSETRACK

END

State=ST_CHOOSETRACK

TEST Master = ST_IDLE

AND testmode = 0

SET Mode 0

SETSTATE ST_IDLE

ELSETEST Master = ST_BEGINBACK

TEST infwdpos = 1

CALC setpoint = posRound + posBackOffset

ELSE

SET setpoint posBackOffset

ENDTEST

SET startpos curpos

CALC distance = setpoint - curpos

TIMEOUT TimeStartMax ST_START

SETSTATE ST_START

ELSETEST Master = ST_BEGINFORWARDSTAY

TEST infwdpos = 1

CALC temp = posRound + posRoundHalf

CALC setpoint = posForwardOffset + temp

ELSE

CALC setpoint = posForwardOffset + posRoundHalf

ENDTEST

SET startpos curpos

CALC distance = setpoint - curpos

TIMEOUT TimeStartMax ST_START

SETSTATE ST_START

ELSETEST Master = ST_BEGINFORWARD

TEST infwdpos = 1

SET setpoint posBackOffset

SET infwdpos 0

ELSE

CALC setpoint = posRound + posBackOffset

SET infwdpos 1

ENDTEST

SET startpos curpos

CALC distance = setpoint - curpos

TIMEOUT TimeStartMax ST_START

SETSTATE ST_START

ELSETEST testmode = 1

TIMEOUT TimeTest ST_TEST

SETSTATE ST_TEST

ENDTEST

END

State=ST_TEST

TEST TimeTest = 1

TEST teststate = 0

SET teststate 1

;forward

TEST infwdpos = 1

SET setpoint posBackOffset

SET infwdpos 0

ELSE

CALC setpoint = posRound + posBackOffset

SET infwdpos 1

ENDTEST

SET startpos curpos

CALC distance = setpoint - curpos

TIMEOUT TimeStartMax ST_START

SETSTATE ST_START

ELSETEST teststate = 1

SET teststate 2

;forwardstay

TEST infwdpos = 1

CALC temp = posRound + posRoundHalf

CALC setpoint = posForwardOffset + temp

ELSE

CALC setpoint = posForwardOffset + posRoundHalf

ENDTEST

SET startpos curpos

CALC distance = setpoint - curpos

TIMEOUT TimeStartMax ST_START

SETSTATE ST_START

ELSETEST teststate = 2

SET teststate 0

;back

TEST infwdpos = 1

CALC setpoint = posRound + posBackOffset

ELSE

SET setpoint posBackOffset

ENDTEST

SET startpos curpos

CALC distance = setpoint - curpos

TIMEOUT TimeStartMax ST_START

SETSTATE ST_START

ENDTEST

ENDTEST

END

State=ST_STOP

SET curpm 1000.0

SETSTATE ST_CHOOSETRACK

END

State=ST_START

SET curpm 0.0

TEST Inpos = 0

OR TimeStartMax = 1

SETSTATE ST_RUN

ENDTEST

END

State=ST_RUN

CALC curpm = curpos - startpos

CALC curpm = curpm / distance

CALC curpm = curpm * 1000.0

TEST Inpos = 1

SETSTATE ST_STOP

ENDTEST

TEST status != 16

AND status != 32

AND status != 48

AND status != 64

AND status != 80

AND status != 0

SET Mode 0

SET homed 0

TIMEOUT TimeCmdDelay ST_IDLE

SETSTATE ST_TIMER

ENDTEST

END

### 708LangBufferSkub.statemachine

STATEMACHINEVERSION 3

Include=cplangbufferskub.statemachine

Name=LangBufferSkub

Link=CamGen ServoSkub

linkValue=curpm ServoSkub

Const=klapindpm 250

Const=klapudpm 850

Timeout=TimeWaitBack 0

;** User section **

STATEMACHINEVERSION 3

Name=LangBufferSkub

;** Input **

Input=klapinde "LangBufferSkub Klap-"

;** Output **

Output=klap "LangBufferSkub Klap"

;** Link **

Link=CamGen CamGenSkub

Link=pstate ProductState

Link=Counter ProductCount

Link=PushPattern

Link=Conveyors ProductConveyors

Link=bplads BufferPlads

Link=parent Parent

;** linkValue **

linkValue=firstRun WorkCell

linkValue=curpm CamGen

linkValue=maxpush PushPattern

linkValue=gettime PushPattern

linkValue=curppp PushPattern

linkValue=timeKlapDown Program

linkValue=bufferstartingup startingup bplads

linkValue=full bplads

linkValue=numofproducts Counter

;** Table **

;** Item **

;** Const **

Const=klapindpm 350

Const=klapudpm 900

;** Value **

Value=numpush 0

Value=remaining 0

Value=startingup 0

Value=forwardstay 0

Value=errorCode 0

;** Timeout **

Timeout=TimeWaitBack 0

Timeout=TimeKlapDown 300000

Timeout=TimeGet 0

State=ST_TIMER

END

State=ST_HALT

END

State=ST_IDLE

SET klap 0

TEST parent = ST_RESET

SET errorCode 0

SETSTATE ST_RESET

ENDTEST

END

State=ST_RESET

SET TimeKlapDown timeKlapDown

TEST firstRun = 1

SET forwardstay 0

SET numpush 0

ENDTEST

SET startingup 1

TEST forwardstay = 0

SET klap 0

SETSTATE ST_BEGINBACK

ELSE

SET klap 1

SET numpush 0

TIMEOUT TimeKlapDown ST_STAY_FINISH

SETSTATE ST_STAY_FINISH

ENDTEST

END

State=ST_STARTUP

SET startingup 0

TEST Counter = ST_RUN

OR Counter = ST_RUN_MANUELT

SETSTATE ST_WAIT

ENDTEST

TEST parent = ST_IDLE

SETSTATE ST_IDLE

ENDTEST

END

State=ST_WAIT

SET klap 1

TEST numofproducts >= curppp

AND Counter = ST_RUN

AND PushPattern = ST_GO

TEST Conveyors = ST_RUN

OR Conveyors = ST_GOSTOP

; start timer

; hvis bånd stopper før timer udløber -> for tæt

SET TimeGet gettime

TIMEOUT TimeGet ST_WAIT2

SETSTATE ST_WAIT2

ELSETEST Conveyors = ST_STOP

SETSTATE ST_WAIT3

ENDTEST

ENDTEST

TEST parent = ST_IDLE

SETSTATE ST_IDLE

ENDTEST

END

State=ST_WAIT2

TEST TimeGet = 1

TEST bplads = ST_WAITPUSH

OR bufferstartingup = 0

AND bplads = ST_GOCLOSE

CALC remaining = maxpush - numpush

TEST remaining <= 1

SETSTATE ST_BEGINFORWARDSTAY

ELSE

SETSTATE ST_BEGINFORWARD

ENDTEST

ENDTEST

ELSETEST Conveyors = ST_STOP

SET errorCode 1011

SETSTATE ST_IDLE

ENDTEST

TEST parent = ST_IDLE

SETSTATE ST_IDLE

ENDTEST

END

State=ST_WAIT3

TEST bplads = ST_WAITPUSH

OR bufferstartingup = 0

AND bplads = ST_GOCLOSE

CALC remaining = maxpush - numpush

TEST remaining <= 1

SETSTATE ST_BEGINFORWARDSTAY

ELSE

SETSTATE ST_BEGINFORWARD

ENDTEST

ENDTEST

TEST parent = ST_IDLE

SETSTATE ST_IDLE

ENDTEST

END

State=ST_BEGINFORWARD

TEST CamGen = ST_START

CALC numpush = numpush + 1

SETSTATE ST_FORWARD

ENDTEST

TEST parent = ST_IDLE

SETSTATE ST_IDLE

ENDTEST

END

State=ST_BEGINFORWARDSTAY

TEST CamGen = ST_START

SET numpush 0

SETSTATE ST_FORWARDSTAY

ENDTEST

TEST parent = ST_IDLE

SETSTATE ST_IDLE

ENDTEST

END

State=ST_FORWARD

TEST curpm > klapindpm

AND curpm < klapudpm

SET klap 0

ELSE

SET klap 1

ENDTEST

TEST CamGen = ST_STOP

SETSTATE ST_WAIT

ENDTEST

TEST CamGen = ST_NOCHOOSETRACK

OR CamGen = ST_IDLE

SETSTATE ST_IDLE

ENDTEST

END

State=ST_FORWARDSTAY

SET klap 1

TEST CamGen = ST_STOP

TIMEOUT TimeKlapDown ST_STAY_FINISH

SETSTATE ST_STAY_FINISH

ENDTEST

TEST CamGen = ST_NOCHOOSETRACK

OR CamGen = ST_IDLE

SETSTATE ST_IDLE

ENDTEST

END

;TimeKlapDown should be < time to open shutters of BufferPlads (which is roughly 350000 us)

State=ST_STAY_FINISH

SET forwardstay 1

SET numpush 0

TEST bplads = ST_OPEN

OR TimeKlapDown = 1

SET forwardstay 0

SET klap 0

TIMEOUT TimeWaitBack ST_BEGINBACK

SETSTATE ST_TIMER

ENDTEST

TEST parent = ST_IDLE

SETSTATE ST_IDLE

ENDTEST

END

State=ST_BEGINBACK

SET klap 0

TEST CamGen = ST_START

SETSTATE ST_GOBACK

ENDTEST

TEST parent = ST_IDLE

SETSTATE ST_IDLE

ENDTEST

END

State=ST_GOBACK

SET klap 0

TEST startingup = 0

AND curpm > klapudpm

SET klap 1

ENDTEST

TEST CamGen = ST_STOP

TEST startingup = 1

SETSTATE ST_STARTUP

ELSE

SETSTATE ST_WAIT

ENDTEST

ENDTEST

TEST CamGen = ST_NOCHOOSETRACK

OR CamGen = ST_IDLE

SETSTATE ST_IDLE

ENDTEST

END

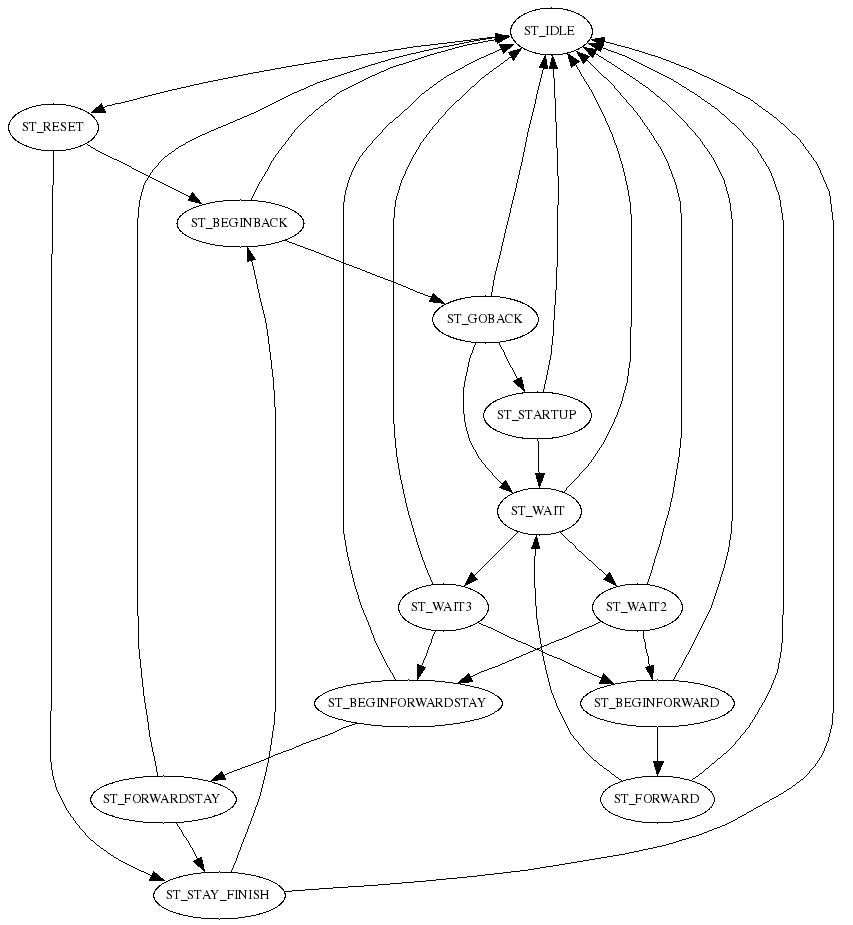
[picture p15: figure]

fig 16: 708LangBufferSkub.statemachine

### 708ServoBuffer.statemachine

STATEMACHINEVERSION 3

Include=cpservobuffer.statemachine

Name=ServoBuffer

;** User section **

Const=home_speed 550.0000

STATEMACHINEVERSION 3

Name=ServoBuffer

Link=Master BufferPlads

fig 17: 708ServoBuffer.statemachine

Link=parent Parent

Input=homesensor "BufferPlads HomeSensor"

Output=Mode "BufferPlads Mode"

Output=setpoint "BufferPlads MacSetpoint"

Output=vsoll "BufferPlads Maxvel"

Output=asoll "BufferPlads Maxacc"

Output=set_curpos "BufferPlads Curpos"

Output=kvout "BufferPlads Load Factor"

Output=set_status "BufferPlads Status"

Input=temperature "BufferPlads Temperature"

Input=Inpos "BufferPlads IN_POS"

Input=curpos "BufferPlads Curpos"

Input=curvel "BufferPlads Curvel"

Input=status "BufferPlads Status"

Value=errorCode 0

Value=curpm 0.0

Const=posBackOffset 3000

Const=posForwardOffset 97000

Const=loadfactor 2.5000

Value=homed 0

Const=homeSensorPol 0

Const=home_speed 400.0000

Const=acceleration 35000.0000

Const=cruise_speed 2700.0000

Const=testmode 0

Value=teststate 0

Value=distance 0.0

Value=startpos 0.0

Timeout=TimeTest 500000

Timeout=TimeCmdDelay 500000

Timeout=TimeStartMax 500000

Timeout=TimeHome 10000000

State=ST_TIMER

END

State=ST_HALT

END

State=ST_IDLE

TEST parent = ST_RESET

TEST status != 16

AND status != 32

AND status != 48

AND status != 64

AND status != 80

AND status != 0

SET set_status 0

ENDTEST

SET errorCode 0

SETSTATE ST_RESET

ENDTEST

END

State=ST_RESET

SET kvout loadfactor

SET asoll acceleration

TEST homed = 0

SET vsoll home_speed

SET Mode 1

TIMEOUT TimeHome ST_HOME

SETSTATE ST_HOME

ELSE

SET vsoll cruise_speed

SET setpoint curpos

TIMEOUT TimeCmdDelay ST_INIT

SETSTATE ST_INIT

ENDTEST

END

State=ST_HOME

TEST homesensor = homeSensorPol

SET Mode 0

TIMEOUT TimeCmdDelay ST_HOME2

SETSTATE ST_HOME2

ELSETEST TimeHome = 1

SET errorCode 1051

SET Mode 0

SETSTATE ST_IDLE

ENDTEST

END

State=ST_HOME2

TEST TimeCmdDelay = 1

SET setpoint 0

SET set_curpos 0

SET homed 1

SET Mode 2

TIMEOUT TimeCmdDelay ST_HOME3

SETSTATE ST_HOME3

ENDTEST

END

State=ST_HOME3

TEST TimeCmdDelay = 1

SET vsoll cruise_speed

SET setpoint posBackOffset

SET startpos curpos

SET distance posBackOffset

TIMEOUT TimeStartMax ST_START

SETSTATE ST_START

ENDTEST

END

State=ST_INIT

TEST TimeCmdDelay = 1

SET Mode 2

SETSTATE ST_CHOOSETRACK

ENDTEST

END

State=ST_NOCHOOSETRACK

END

State=ST_CHOOSETRACK

TEST Master = ST_IDLE

AND testmode = 0

SET Mode 0

SETSTATE ST_IDLE

ELSETEST Master = ST_BEGINCLOSE

SET setpoint posBackOffset

SET startpos curpos

CALC distance = setpoint - curpos

TIMEOUT TimeStartMax ST_START

SETSTATE ST_START

ELSETEST Master = ST_BEGINOPEN

SET setpoint posForwardOffset

SET startpos curpos

CALC distance = setpoint - curpos

TIMEOUT TimeStartMax ST_START

SETSTATE ST_START

ELSETEST testmode = 1

TIMEOUT TimeTest ST_TEST

SETSTATE ST_TEST

ENDTEST

END

State=ST_TEST

TEST TimeTest = 1

TEST teststate = 0

SET teststate 1

;forward

SET setpoint posForwardOffset

SET startpos curpos

CALC distance = setpoint - curpos

TIMEOUT TimeStartMax ST_START

SETSTATE ST_START

ELSETEST teststate = 1

SET teststate 0

;back

SET setpoint posBackOffset

SET startpos curpos

CALC distance = setpoint - curpos

TIMEOUT TimeStartMax ST_START

SETSTATE ST_START

ENDTEST

ENDTEST

END

State=ST_STOP

SET curpm 1000.0

SETSTATE ST_CHOOSETRACK

END

State=ST_START

SET curpm 0.0

TEST Inpos = 0

OR TimeStartMax = 1

SETSTATE ST_RUN

ENDTEST

END

State=ST_RUN

CALC curpm = curpos - startpos

CALC curpm = curpm / distance

CALC curpm = curpm * 1000.0

TEST Inpos = 1

SETSTATE ST_STOP

ENDTEST

TEST status != 16

AND status != 32

AND status != 48

AND status != 64

AND status != 80

AND status != 0

SET Mode 0

SET homed 0

TIMEOUT TimeCmdDelay ST_IDLE

SETSTATE ST_TIMER

ENDTEST

END

### 708BufferPlads.statemachine

STATEMACHINEVERSION 3

Include=cpbufferplads.statemachine

Name=BufferPlads

Link=CamGen ServoBuffer

Link=CemGenSkub ServoSkub

Link=CamGenLift ServoLift

linkValue=curpmskub curpm ServoSkub

linkValue=liftFree ServoLift

;** User section **

Timeout=WaitLeftRightKortSkub 300000

Timeout=WaitKortSkub 100000

STATEMACHINEVERSION 3

Name=BufferPlads

;** Input **

Input=kortskubleftinde "KortBufferSkub Left Inde"

Input=kortskubrightinde "KortBufferSkub Right Inde"

;** Output **

Output=kortskubleft1 "KortBufferSkubber Left 1"

Output=kortskubleft2 "KortBufferSkubber Left 2"

Output=kortskubright1 "KortBufferSkubber Right 1"

Output=kortskubright2 "KortBufferSkubber Right 2"

;** Link **

Link=KasseLift

Link=CamGen CamGenBuffer

Link=CamGenSkub

Link=CamGenLift

Link=Skubber LangBufferSkub

;** linkValue **

linkValue=firstRun WorkCell

linkValue=curpmskub curpm CamGenSkub

linkValue=liftFree CamGenLift

linkValue=pushshortleft PushPattern

linkValue=pushshortright PushPattern

linkValue=numpush LangBufferSkub

linkValue=layers KasseLift

linkValue=maxlayers PushPattern

;** Const **

Const=KortSkubpm 900

;** Value **

Value=full 0

Value=startingup 0

Value=emptyflag 0

Value=bufferlayers 0

;** Timeout **

Timeout=WaitKortSkub 100000

Timeout=WaitLeftRightKortSkub 300000

Timeout=TimeOpen 0

State=ST_TIMER

END

State=ST_HALT

END

State=ST_IDLE

SET kortskubleft1 0

SET kortskubleft2 0

SET kortskubright1 0

SET kortskubright2 0

TEST Skubber = ST_RESET

SETSTATE ST_RESET

ENDTEST

END

State=ST_RESET

TEST firstRun = 1

SET full 0

SET emptyflag 0

SET bufferlayers 0

ENDTEST

SET startingup 1

TEST CamGen = ST_CHOOSETRACK

SETSTATE ST_BEGINCLOSE

ENDTEST

TEST Skubber = ST_IDLE

SETSTATE ST_IDLE

ENDTEST

END

State=ST_STARTUP

SET startingup 0

TEST full = 0

SETSTATE ST_WAITPUSH

ELSE

SET kortskubleft1 1

SET kortskubleft2 1

SET kortskubright1 1

SET kortskubright2 1

TIMEOUT WaitKortSkub ST_DUMP

SETSTATE ST_DUMP

ENDTEST

END

State=ST_WAITPUSH

TEST Skubber = ST_FORWARD

SETSTATE ST_GETPUSH

ELSE

TEST Skubber = ST_FORWARDSTAY

SETSTATE ST_GETFULL

ENDTEST

ENDTEST

TEST Skubber = ST_IDLE

SETSTATE ST_IDLE

ENDTEST

END

State=ST_GETPUSH

TEST curpmskub > 500

TEST numpush = pushshortleft

AND pushshortleft != 0

SET kortskubleft1 1

SET kortskubleft2 1

TIMEOUT WaitLeftRightKortSkub ST_PUSHSHORT

SETSTATE ST_PUSHSHORT

ENDTEST

TEST numpush = pushshortright

AND pushshortright != 0

SET kortskubright1 1

SET kortskubright2 1

TIMEOUT WaitLeftRightKortSkub ST_PUSHSHORT

SETSTATE ST_PUSHSHORT

ENDTEST

ENDTEST

TEST Skubber != ST_FORWARD

SETSTATE ST_WAITPUSH

ENDTEST

END

State=ST_PUSHSHORT

TEST WaitLeftRightKortSkub = 1

SET kortskubleft1 0

SET kortskubleft2 0

SET kortskubright1 0

SET kortskubright2 0

ENDTEST

TEST Skubber != ST_FORWARD

SET kortskubleft1 0

SET kortskubleft2 0

SET kortskubright1 0

SET kortskubright2 0

SETSTATE ST_WAITPUSH

ENDTEST

END

State=ST_GETFULL

TEST curpmskub > KortSkubpm

SET kortskubleft1 1

SET kortskubleft2 1

SET kortskubright1 1

SET kortskubright2 1

ENDTEST

TEST Skubber = ST_STAY_FINISH

SET full 1

CALC bufferlayers = layers + 1

TEST bufferlayers >= maxlayers

SET bufferlayers 0

ENDTEST

SET emptyflag 0

SET kortskubleft1 1

SET kortskubleft2 1

SET kortskubright1 1

SET kortskubright2 1

TIMEOUT WaitKortSkub ST_DUMP

SETSTATE ST_DUMP

ENDTEST

END

State=ST_DUMP

TEST CamGen = ST_CHOOSETRACK

TEST WaitKortSkub = 1

SET kortskubleft1 1

SET kortskubleft2 0

SET kortskubright1 1

SET kortskubright2 0

TEST KasseLift = ST_READY2

SETSTATE ST_BEGINOPEN

ELSE

TEST liftFree = 0

AND KasseLift = ST_GO

SETSTATE ST_BEGINOPEN

ENDTEST

ENDTEST

ENDTEST

ENDTEST

TEST Skubber = ST_IDLE

SETSTATE ST_IDLE

ENDTEST

END

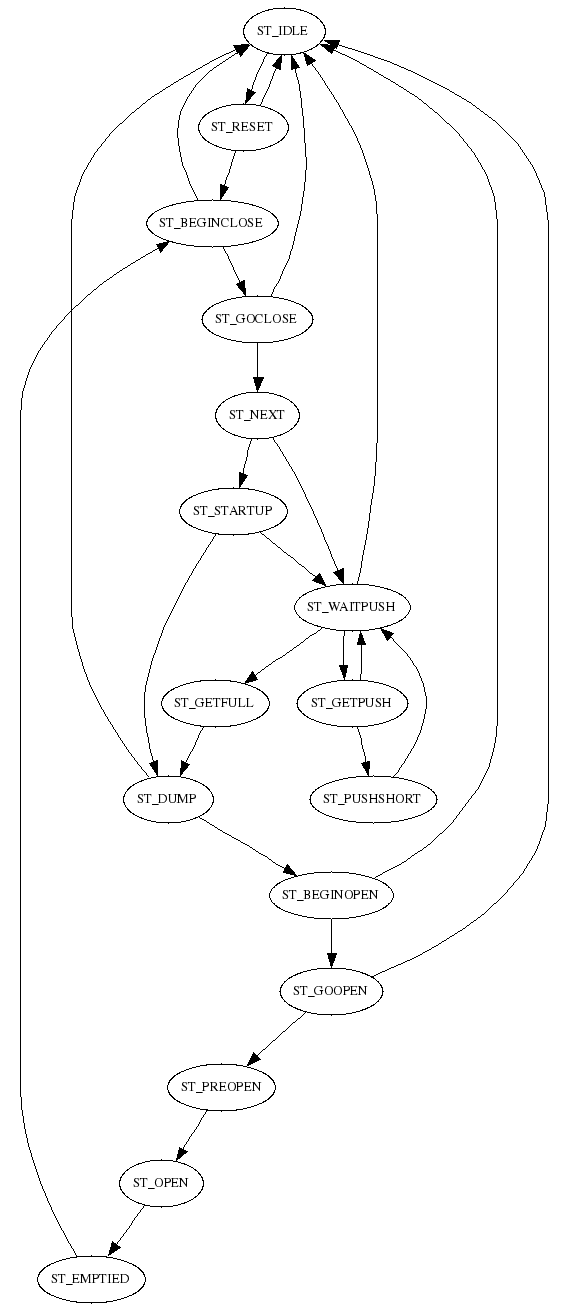
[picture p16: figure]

fig 18: 708BufferPlads.statemachine

State=ST_BEGINOPEN

TEST CamGen = ST_START

SETSTATE ST_GOOPEN

ELSE

TEST Skubber = ST_IDLE

SETSTATE ST_IDLE

ENDTEST

ENDTEST

END

State=ST_GOOPEN

TEST CamGen = ST_STOP

SET full 0

SETSTATE ST_PREOPEN

ENDTEST

TEST CamGen = ST_NOCHOOSETRACK

OR CamGen = ST_IDLE

SETSTATE ST_IDLE

ENDTEST

END

State=ST_PREOPEN

TEST KasseLift = ST_READY2

OR KasseLift = ST_IDLE

TIMEOUT TimeOpen ST_OPEN

SETSTATE ST_OPEN

ENDTEST

END

State=ST_OPEN

TEST TimeOpen = 1

SETSTATE ST_EMPTIED

ENDTEST

END

State=ST_EMPTIED

SET emptyflag 1

TEST liftFree = 1

OR KasseLift = ST_IDLE

TEST CamGen = ST_CHOOSETRACK

SETSTATE ST_BEGINCLOSE

ENDTEST

ENDTEST

END

State=ST_BEGINCLOSE

SET kortskubleft1 0

SET kortskubleft2 0

SET kortskubright1 0

SET kortskubright2 0

TEST CamGen = ST_START

SETSTATE ST_GOCLOSE

ELSE

TEST Skubber = ST_IDLE

SETSTATE ST_IDLE

ENDTEST

ENDTEST

END

State=ST_GOCLOSE

TEST CamGen = ST_STOP

SETSTATE ST_NEXT

ENDTEST

TEST CamGen = ST_NOCHOOSETRACK

OR CamGen = ST_IDLE

SETSTATE ST_IDLE

ENDTEST

END

State=ST_NEXT

TEST kortskubleftinde = 1

AND kortskubrightinde = 1

TEST startingup = 0

SETSTATE ST_WAITPUSH

ELSE

SETSTATE ST_STARTUP

ENDTEST

ENDTEST

END

### 708ServoLift.statemachine

STATEMACHINEVERSION 3

Include=cpservolift.statemachine

Name=ServoLift

;** User section **

Const=posTop 345.0000

STATEMACHINEVERSION 3

Name=ServoLift

Link=Master KasseLift

Link=parent Parent

linkValue=firstRun WorkCell

linkValue=inShake Master

Output=home_vel "KasseLift Homevel"

Output=home_tq "KasseLift Hometorque"

Output=Mode "KasseLift Mode"

Output=setpoint "KasseLift MacSetpoint"

Output=vsoll "KasseLift Maxvel"

Output=asoll "KasseLift Maxacc"

Output=set_curpos "KasseLift Curpos"

Output=kvout "KasseLift Load Factor"

Output=tsoll "KasseLift Maxtorque"

Output=set_status "KasseLift Status"

;Output=reset_homedone "KasseLift Reset Home_Done"

Input=temperature "KasseLift Temperature"

Input=Inpos "KasseLift IN_POS"

Input=curpos "KasseLift Curpos"

Input=curtorque "KasseLift Curtorque"

Input=homedone "KasseLift HOME_DONE"

Input=curtsoll "KasseLift Maxtorque"

Input=status "KasseLift Status"

;Input=flwerr "KasseLift Follow Error"

;Input=fncerr "KasseLift Function Error"

Value=errorCode 0

Value=curpm 0.0

Const=loadfactor 3.0000

Value=homed 0

Value=temp 0

Const=home_speed -250.0000

Const=home_torque -50.0000

Const=acceleration 15000.0000

Const=cruise_speed 3000.0000

Const=testmode 0

Value=teststate 0

Value=distance 0.0

Value=startpos 0.0

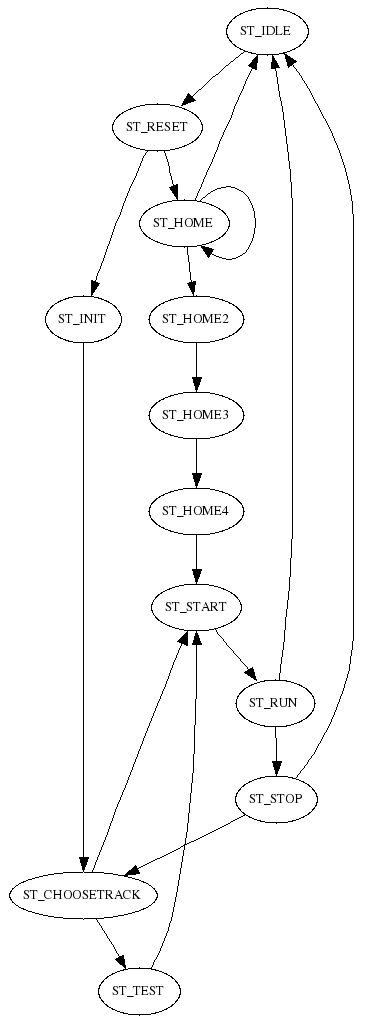
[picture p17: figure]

fig 19: 708ServoLift.statemachine

Value=posf 0.0

Value=goIdle 0

Value=liftFree 1

Value=staticmode 0

;jogmode is controlled from formJogLiftUser.c

Value=jogmode 0

; tickspermotorround*gearudveksling/(eff_rad*2*pi)

; eks: 8000*13.3/(27.5*2*pi)

Const=tickspermm 615.7849434537

; All posXX in mm.

Const=posHome 10.0

;posShake > posFree

Const=posShake 70.0000

Const=posFree 60.0000

Const=posTop 378.0000

Const=posTestBegin 100.0000

Const=posTestEnd 157.0000

linkValue=item Program

Timeout=TimeTest 0

Timeout=TimeCmdDelay 500000

Timeout=TimeStartMax 1000000

Timeout=TimeHome 20000000

Timeout=TimeStatic 5000000

State=ST_TIMER

END

State=ST_HALT

END

State=ST_IDLE

TEST parent = ST_RESET

TEST status != 16

AND status != 32

AND status != 48

AND status != 64

AND status != 80

AND status != 0

; SET homed 0

SET set_status 0

ENDTEST

SET Mode 0

SET errorCode 0

TIMEOUT TimeCmdDelay ST_RESET

SETSTATE ST_TIMER

ENDTEST

END

State=ST_RESET

CALC posf = posTop - item.dy

CALC posf = posf - posFree

CALC posf = posf * tickspermm

SET kvout loadfactor

SET asoll acceleration

TEST homed = 0

SET home_vel home_speed

SET home_tq home_torque

SET temp 0

TIMEOUT TimeCmdDelay ST_HOME

SETSTATE ST_HOME

ELSE

SET vsoll cruise_speed

SET setpoint curpos

TIMEOUT TimeCmdDelay ST_INIT

SETSTATE ST_INIT

ENDTEST

END

State=ST_HOME

TEST temp = 0

AND TimeCmdDelay = 1

SET Mode 12

SET temp 1

TIMEOUT TimeCmdDelay ST_HOME

SETSTATE ST_HOME

ELSETEST temp = 1

AND TimeCmdDelay = 1

SET temp 2

TIMEOUT TimeHome ST_HOME

SETSTATE ST_HOME

ELSETEST temp = 2

TEST homedone = 1

SET homed 1

SET Mode 0

SET vsoll cruise_speed

TIMEOUT TimeCmdDelay ST_HOME2

SETSTATE ST_HOME2

ELSETEST TimeHome = 1

SET errorCode 1052

SET Mode 0

SETSTATE ST_IDLE

ENDTEST

ENDTEST

END

State=ST_HOME2

TEST TimeCmdDelay = 1

SET setpoint curpos

TIMEOUT TimeCmdDelay ST_HOME3

SETSTATE ST_HOME3

ENDTEST

END

State=ST_HOME3

TEST TimeCmdDelay = 1

SET Mode 2

TIMEOUT TimeCmdDelay ST_HOME4

SETSTATE ST_HOME4

ENDTEST

END

State=ST_HOME4

TEST TimeCmdDelay = 1

CALC setpoint = tickspermm * posHome

SET startpos curpos

CALC distance = setpoint - curpos

TIMEOUT TimeStartMax ST_START

SETSTATE ST_START

ENDTEST

END

State=ST_INIT

TEST TimeCmdDelay = 1

SET Mode 2

TIMEOUT TimeStatic ST_CHOOSETRACK

SETSTATE ST_CHOOSETRACK

ENDTEST

END

State=ST_NOCHOOSETRACK

END

State=ST_CHOOSETRACK

TEST Master = ST_BEGINHOME

CALC setpoint = tickspermm * posHome

SET startpos curpos

CALC distance = setpoint - curpos

TIMEOUT TimeStartMax ST_START

SETSTATE ST_START

ELSETEST Master = ST_BEGINHIGH

CALC temp = posTop - item.dy

TEST inShake = 1

CALC temp = temp - posShake

ENDTEST

CALC setpoint = tickspermm * temp

SET startpos curpos

CALC distance = setpoint - curpos

TIMEOUT TimeStartMax ST_START

SETSTATE ST_START

ELSETEST testmode = 1

TIMEOUT TimeTest ST_TEST

SETSTATE ST_TEST

ELSETEST staticmode = 0

AND TimeStatic = 1

SET Mode 0

SET staticmode 1

ENDTEST

TEST Master = ST_IDLE

AND testmode = 0

AND jogmode = 0

SET goIdle 1

CALC setpoint = tickspermm * posHome

SET startpos curpos

CALC distance = setpoint - curpos

TIMEOUT TimeStartMax ST_START

SETSTATE ST_START

ENDTEST

TEST curpos < posf

SET liftFree 1

ELSE

SET liftFree 0

ENDTEST

END

State=ST_TEST

TEST TimeTest = 1

TEST teststate = 0

SET teststate 1

CALC setpoint = tickspermm * posTestBegin

SET startpos curpos

CALC distance = setpoint - curpos

TIMEOUT TimeStartMax ST_START

SETSTATE ST_START

ELSETEST teststate = 1

SET teststate 0

CALC temp = posTop - item.dy

CALC setpoint = tickspermm * temp

;CALC setpoint = tickspermm * posTestEnd

SET startpos curpos

CALC distance = setpoint - curpos

TIMEOUT TimeStartMax ST_START

SETSTATE ST_START

ENDTEST

ENDTEST

TEST curpos < posf

SET liftFree 1

ELSE

SET liftFree 0

ENDTEST

END

State=ST_STOP

SET curpm 1000.0

TEST Master = ST_IDLE

AND goIdle = 1

SET goIdle 0

SET Mode 0

SETSTATE ST_IDLE

ELSE

TIMEOUT TimeStatic ST_CHOOSETRACK

SETSTATE ST_CHOOSETRACK

ENDTEST

END

State=ST_START

SET curpm 0.0

TEST staticmode = 1

SET Mode 2

SET staticmode 0

ENDTEST

TEST Inpos = 0

OR TimeStartMax = 1

SETSTATE ST_RUN

ENDTEST

TEST curpos < posf

SET liftFree 1

ELSE

SET liftFree 0

ENDTEST

END

State=ST_RUN

CALC curpm = curpos - startpos

CALC curpm = curpm / distance

CALC curpm = curpm * 1000.0

TEST Inpos = 1

SETSTATE ST_STOP

ENDTEST

TEST curpos < posf

SET liftFree 1

ELSE

SET liftFree 0

ENDTEST

TEST status != 16

AND status != 32

AND status != 48

AND status != 64

AND status != 80

AND status != 0

SET Mode 0

; SET homed 0

TIMEOUT TimeCmdDelay ST_IDLE

SETSTATE ST_TIMER

ENDTEST

END

### 708KasseLift.statemachine

STATEMACHINEVERSION 3

Include=cpkasselift.statemachine

Name=KasseLift

Output=Kassestop "KasseStop 1"

Link=CamGen ServoLift

;** User section **

STATEMACHINEVERSION 3

Name=KasseLift

;** Input **

;** Output **

Output=Centrer "KasseCentrer"

Output=Kassestop "dummyOut"

Output=Kassestop1 "dummyOut"

Output=Motor "KasseLift Conveyor Motor"

;** Link **

Link=CamGen CamGenLift

Link=parent Parent

Link=KasseInLiner

Link=BufferPlads

Link=next KasseLiftNext

Link=Foto KasseLiftFoto

Link=FotoFree KasseFreeFoto

Link=vibrator Vibrator

;** linkValue **

linkValue=firstRun WorkCell

linkValue=Fototest test Foto

linkValue=fotofree test FotoFree

linkValue=maxlayers PushPattern

linkValue=timeMotorInGoDown Program

linkValue=noShakeOnLast Program

linkValue=waitInR3 Program

linkValue=kasseStopType Program

linkValue=full BufferPlads

linkValue=emptyflag BufferPlads

linkValue=manuelt Program

linkValue=canSend recv1 next

linkValue=kassestoppos gostoppos ServoStop

Link=ServoStop

;** Table **

;** Item **

;** Const **

Const=centerOutInShake 0

Const=useFotoFree 0

;** Value **

Value=errorCode 0

Value=layers 0

Value=curshake 0

Value=reboot 0

Value=startingup 0

Value=inShake 0

Value=temp 0.0

Value=sending 0

Value=centered 0

Value=testmode 0

Value=simulate 0

;** Timeout **

Timeout=KStopDelay 2000000

Timeout=TimeStartUp 4000000

Timeout=TimeWaitShake 300000

Timeout=TimeSend 10000000

Timeout=TimePapMotor 0

Timeout=TimeW3 3000000

Timeout=testTime 3000000

Timeout=minSendTime 500000

Timeout=TimeCenter 1100000

Timeout=TimeInCenter 1000000

Timeout=timeCentrerOut 300000

Timeout=timeWaitForServoStop 2000000

; reboot = 0 -> ren rÃ¸v

; reboot = 1 -> starter med tom kasse

; reboot = 2 -> starter med fyldt kasse

State=ST_TIMER

END

State=ST_HALT

END

State=ST_IDLE

SET Centrer 0

SET kassestoppos 0

SET Kassestop 0

SET Kassestop1 0

SET Motor 0

TEST parent = ST_RESET

AND manuelt = 0

SETSTATE ST_RESET

ENDTEST

TEST simulate = 1

SETSTATE ST_RESET

ENDTEST

END

State=ST_RESET

SET errorCode 0

TEST firstRun = 1

SET reboot 0

SET layers 0

ENDTEST

SET curshake 0

SET inShake 0

SET startingup 1

SET Motor 0

TEST CamGen = ST_CHOOSETRACK

AND ServoStop != ST_HOME

AND ServoStop != ST_HOME2

AND ServoStop != ST_HOME3

AND ServoStop != ST_HOME4

TIMEOUT timeWaitForServoStop ST_BEGINHOME

SETSTATE ST_TIMER

ENDTEST

TEST parent = ST_IDLE

AND simulate = 0

SETSTATE ST_IDLE

ENDTEST

END

State=ST_STARTUP

SET startingup 0

TEST Foto = ST_OFF

TEST reboot = 1

SETSTATE ST_READY1

ELSE

TEST reboot = 2

TIMEOUT TimeW3 ST_READY

SETSTATE ST_READY

ELSE

TEST reboot = 0

TIMEOUT KStopDelay ST_PREPARE_SEARCHBOX

SETSTATE ST_PREPARE_SEARCHBOX

ENDTEST

ENDTEST

ENDTEST

ELSE

TEST Foto = ST_ON

TEST reboot = 0

SETSTATE ST_EMPTY

ELSE

TIMEOUT KStopDelay ST_PREPARE_SEARCHBOX

SETSTATE ST_PREPARE_SEARCHBOX

ENDTEST

ENDTEST

ENDTEST

TEST parent = ST_IDLE

AND simulate = 0

SETSTATE ST_IDLE

ENDTEST

END

State=ST_PREPARE_SEARCHBOX

SET Centrer 0

TEST kasseStopType = 1

SET Kassestop 1

SET Kassestop1 0

ELSETEST kasseStopType = 2

SET Kassestop 1

SET Kassestop1 1

ELSETEST kasseStopType = 3

SET kassestoppos 1

ENDTEST

TEST KStopDelay = 1

TIMEOUT TimeStartUp ST_SEARCHBOX

SETSTATE ST_SEARCHBOX

ENDTEST

END

State=ST_SEARCHBOX

SET Motor 1

TEST TimeStartUp = 1

SET reboot 0

SETSTATE ST_STARTUP

ENDTEST

TEST Fototest = 0

TEST simulate = 1

SETSTATE ST_SEND

ELSE

SET reboot 1

SETSTATE ST_STARTUP

ENDTEST

ENDTEST

TEST parent = ST_IDLE

AND simulate = 0

SETSTATE ST_IDLE

ENDTEST

END

State=ST_EMPTY

SET Centrer 0

TEST kasseStopType = 1

SET Kassestop 1

SET Kassestop1 0

ELSETEST kasseStopType = 2

SET Kassestop 1

SET Kassestop1 1

ELSETEST kasseStopType = 3

SET kassestoppos 1

ENDTEST

TEST KasseInLiner = ST_SEND

SET Motor 1

SET centered 0

TIMEOUT TimeCenter ST_RECEIVE

SETSTATE ST_RECEIVE

ELSE

SET Motor 0

ENDTEST

TEST parent = ST_IDLE

AND simulate = 0

SETSTATE ST_IDLE

ENDTEST

END

State=ST_RECEIVE

SET Motor 1

TEST centered = 0

TEST TimeCenter = 1

SET Centrer 1

SET centered 1

TIMEOUT TimeInCenter ST_RECEIVE

SETSTATE ST_RECEIVE

ENDTEST

ELSE

TEST TimeInCenter = 1

AND centered = 1

SET Centrer 0

SET centered 2

ENDTEST

ENDTEST

TEST Fototest = 0

SET Centrer 1

SET Motor 0

SET reboot 1

TEST simulate = 1

SETSTATE ST_SEND

ELSE

SETSTATE ST_READY1

ENDTEST

ENDTEST

TEST KasseInLiner = ST_IDLE

SETSTATE ST_IDLE

ENDTEST

END

State=ST_READY1

SET Motor 0

SET Centrer 1

TEST CamGen = ST_CHOOSETRACK

SETSTATE ST_BEGINHIGH

ENDTEST

TEST parent = ST_IDLE

AND simulate = 0

SETSTATE ST_IDLE

ENDTEST

END

State=ST_READY2

SET kassestoppos 0

SET Kassestop 0

SET Kassestop1 0

TEST BufferPlads = ST_OPEN

CALC layers = layers + 1

TEST layers >= maxlayers

SET layers 0

ENDTEST

SETSTATE ST_SHAKE1

ENDTEST

TEST parent = ST_IDLE

AND simulate = 0

SETSTATE ST_IDLE

ENDTEST

END

State=ST_SHAKE1

TEST layers = 0

AND noShakeOnLast = 1

SETSTATE ST_SHAKEDONE

ELSE

TEST CamGen = ST_CHOOSETRACK

SET inShake 1

TEST centerOutInShake = 1

SET Centrer 0

ENDTEST

SETSTATE ST_BEGINHIGH

ELSE

TEST CamGen = ST_NOCHOOSETRACK

OR CamGen = ST_IDLE

SETSTATE ST_IDLE

ENDTEST

ENDTEST

ENDTEST

END

State=ST_SHAKE2

TEST emptyflag = 1

TIMEOUT TimeWaitShake ST_SHAKE3

SETSTATE ST_SHAKE3

ENDTEST

END

State=ST_SHAKE3

TEST TimeWaitShake = 1

SET inShake 2

TEST CamGen = ST_CHOOSETRACK

SETSTATE ST_BEGINHIGH

ELSE

TEST CamGen = ST_NOCHOOSETRACK

OR CamGen = ST_IDLE

SETSTATE ST_IDLE

ENDTEST

ENDTEST

ENDTEST

END

State=ST_SHAKEDONE

SET inShake 0

TEST centerOutInShake = 1

SET Centrer 1

ENDTEST

TEST layers = 0

SET reboot 2

SETSTATE ST_GODOWN

ELSE

SETSTATE ST_READY2

ENDTEST

END

State=ST_GODOWN

TEST timeMotorInGoDown != 0

SET Centrer 0

ENDTEST

TEST CamGen = ST_CHOOSETRACK

SET TimePapMotor timeMotorInGoDown

TIMEOUT TimePapMotor ST_BEGINHOME

SETSTATE ST_BEGINHOME

ELSE

TEST CamGen = ST_NOCHOOSETRACK

OR CamGen = ST_IDLE

SETSTATE ST_IDLE

ENDTEST

ENDTEST

END

State=ST_READY

SET kassestoppos 0

SET Kassestop 0

SET Kassestop1 0

TEST vibrator = ST_GO

SET Centrer 1

ELSE

SET Centrer 0

ENDTEST

TEST waitInR3 = 0

OR TimeW3 = 1

TEST next = ST_EMPTY

AND canSend = 1

SET Centrer 0

TIMEOUT timeCentrerOut ST_SEND

SETSTATE ST_SEND

ENDTEST

ENDTEST

TEST parent = ST_IDLE

AND simulate = 0

SETSTATE ST_IDLE

ENDTEST

END

State=ST_SEND

TEST sending = 0

SET Centrer 0

TEST timeCentrerOut = 1

TEST next = ST_RECEIVE

OR simulate = 1

SET sending 1

SET Motor 1

TIMEOUT minSendTime ST_SEND

SETSTATE ST_SEND

ENDTEST

ENDTEST

ELSE

TEST sending = 1

TEST minSendTime = 1

SET sending 2

TIMEOUT TimeSend ST_SEND

SETSTATE ST_SEND

ENDTEST

ELSE

TEST sending = 2

TEST Fototest = 1

AND useFotoFree = 0

SET sending 0

SET reboot 0

SETSTATE ST_EMPTY

ENDTEST

TEST fotofree = 1

AND useFotoFree = 1

SET sending 0

SET reboot 0

SETSTATE ST_EMPTY

ENDTEST

TEST TimeSend = 1

SET sending 0

SET errorCode 1014

SETSTATE ST_IDLE

ENDTEST

ENDTEST

ENDTEST

ENDTEST

END

State=ST_BEGINHOME

TEST CamGen = ST_START

SETSTATE ST_GO

ELSE

TEST CamGen = ST_NOCHOOSETRACK

OR CamGen = ST_IDLE

SETSTATE ST_IDLE

ENDTEST

ENDTEST

END

State=ST_TESTMODE

TEST testTime = 1

AND CamGen = ST_CHOOSETRACK

SET startingup 0

SET inShake 0

SET reboot 2

SETSTATE ST_BEGINHOME

ENDTEST

TEST parent = ST_IDLE

AND simulate = 0

SETSTATE ST_IDLE

ENDTEST

END

State=ST_BEGINHIGH

TEST CamGen = ST_START

TEST testmode = 1

TIMEOUT testTime ST_TESTMODE

SETSTATE ST_TESTMODE

ELSE

SETSTATE ST_GO

ENDTEST

ELSE

TEST CamGen = ST_NOCHOOSETRACK

OR CamGen = ST_IDLE

SETSTATE ST_IDLE

ENDTEST

ENDTEST

END

State=ST_GO

TEST reboot = 2

CALC temp = timeMotorInGoDown * 0.8

TEST TimePapMotor < temp

SET Motor 1

ENDTEST

TEST TimePapMotor = 1

SET Motor 0

ENDTEST

ENDTEST

TEST CamGen = ST_STOP

TEST startingup = 1

SETSTATE ST_STARTUP

ELSE

TEST inShake = 1

SETSTATE ST_SHAKE2

ELSE

TEST inShake = 2

SETSTATE ST_SHAKEDONE

ELSE

TEST reboot = 1

SETSTATE ST_READY2

ELSE

TEST reboot = 2

SET Motor 0

TIMEOUT TimeW3 ST_READY

SETSTATE ST_READY

ENDTEST

ENDTEST

ENDTEST

ENDTEST

ENDTEST

ENDTEST

TEST CamGen = ST_NOCHOOSETRACK

OR CamGen = ST_IDLE

SETSTATE ST_IDLE

ENDTEST

END

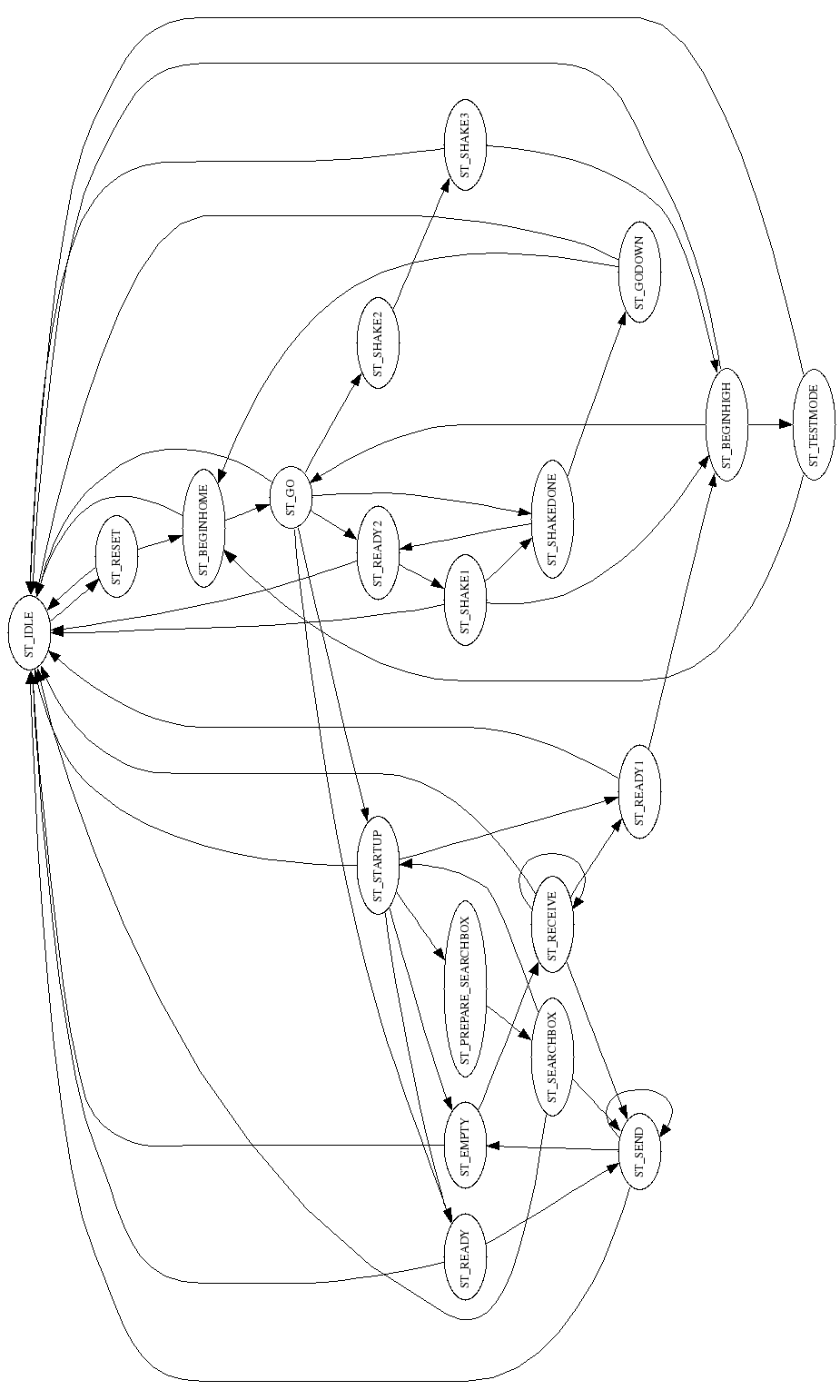
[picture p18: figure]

fig 20: 708KasseLift.statemachine

## Kasse Handling Statemachines

### 708KasseLiftNext.statemachine

STATEMACHINEVERSION 3

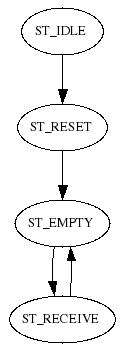
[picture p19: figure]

fig 21: 708KasseLiftNext.statemachine

Name=KasseLiftNext

Link=prev KasseLift

Value=recv1 1

State=ST_TIMER

END

State=ST_HALT

END

State=ST_IDLE

SETSTATE ST_RESET

END

State=ST_RESET

SETSTATE ST_EMPTY

END

State=ST_EMPTY

TEST prev = ST_SEND

SETSTATE ST_RECEIVE

ENDTEST

END

State=ST_RECEIVE

TEST prev != ST_SEND

SETSTATE ST_EMPTY

ENDTEST

END

### 708KasseLiftFoto.statemachine

STATEMACHINEVERSION 3

Include=input.statemachine

Name=KasseLiftFoto

Input=input "KasseLift Foto"

Timeout=TimeOn 250000

Timeout=TimeOff 650000

Value=test 0

Link=parent Parent

### 708KasseLoaderFoto.statemachine

STATEMACHINEVERSION 3

Include=fotoinput.statemachine

Name=KasseLoaderFoto

Input=input "KasseLoader Foto"

Timeout=blockTime 700000

Timeout=freeTime 100000

Value=test 0

Const=free 1

Const=blocked 0

STATEMACHINEVERSION 3

Name=FotoInput

Input=input "dummyOff"

Timeout=blockTime 100000

Timeout=freeTime 100000

Value=test 0

Const=free 0

Const=blocked 1

State=ST_HALT

SETSTATE ST_IDLE

END

State=ST_TIMER

END

State=ST_IDLE

TEST input = blocked

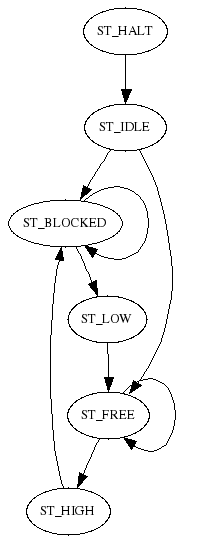
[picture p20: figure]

fig 22: fotoinput.statemachine

SET test blocked

SETSTATE ST_BLOCKED

ELSE

TEST input = free

SET test free

SETSTATE ST_FREE

ENDTEST

ENDTEST

END

State=ST_FREE

TEST input = blocked

AND test = free

SET test blocked

TIMEOUT blockTime ST_FREE

SETSTATE ST_FREE

ENDTEST

TEST input = blocked

AND test = blocked

AND blockTime = 1

SETSTATE ST_HIGH

ENDTEST

TEST input = free

SET test free

ENDTEST

END

State=ST_HIGH

SETSTATE ST_BLOCKED

END

State=ST_BLOCKED

TEST input = free

AND test = blocked

SET test free

TIMEOUT freeTime ST_BLOCKED

SETSTATE ST_BLOCKED

ENDTEST

TEST input = free

AND test = free

AND freeTime = 1

SETSTATE ST_LOW

ENDTEST

TEST input = blocked

SET test blocked

ENDTEST

END

State=ST_LOW

SETSTATE ST_FREE

END

### 708KasseLoader.statemachine

STATEMACHINEVERSION 3

Name=KasseLoader

Output=motor "KasseLoader Motor"

Output=skubber "KasseSkubber1"

;minihack: if Kasseloader doesn't have a stopper set it to any or empty output and set hasStopper = 0, the output will then not be set

linkValue=firstRun WorkCell

Link=skubberReceiver KasseInLiner

;conveyorReceiver only used if hasStopper = 1

Link=conveyorReceiver KasseLoader

Link=foto KasseLoaderFoto

Const=hasStopper 0

;whether or not prev sends from side or back of KasseLoader

Const=sideReceive 0

Timeout=skubberTime 200000

Timeout=motorStopTime 600000

Timeout=maxReceiveTime 999999999

Timeout=startupTime 3000000

Value=gotCase 0

Link=parent Parent

State=ST_GOBACK

SET skubber 0

TEST foto = ST_FREE

SETSTATE ST_EMPTY

ENDTEST

END

State=ST_TIMER

END

State=ST_HALT

END

State=ST_IDLE

SET skubber 0

SET motor 0

TEST parent = ST_RESET

SETSTATE ST_RESET

ENDTEST

END

State=ST_RESET

TEST foto = ST_BLOCKED

TIMEOUT motorStopTime ST_READY

SETSTATE ST_READY

ELSE

TEST foto = ST_FREE

TIMEOUT startupTime ST_STARTUP

SETSTATE ST_STARTUP

ENDTEST

ENDTEST

END

State=ST_STARTUP

TEST firstRun = 1

OR gotCase = 1

TEST startupTime = 1

SETSTATE ST_EMPTY

ELSE

TEST foto = ST_BLOCKED

TIMEOUT motorStopTime ST_READY

SETSTATE ST_READY

ELSE

SET motor 1

ENDTEST

ENDTEST

ELSE

SETSTATE ST_EMPTY

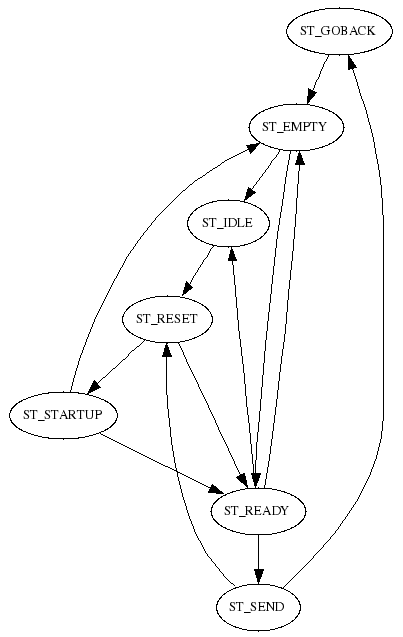
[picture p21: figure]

fig 23: 708KasseLoader.statemachine

ENDTEST

END

State=ST_EMPTY

SET skubber 0

SET motor 1

TEST foto = ST_BLOCKED

TIMEOUT motorStopTime ST_READY

SETSTATE ST_READY

ENDTEST

TEST parent = ST_IDLE

SETSTATE ST_IDLE

ENDTEST

END

State=ST_SEND

SET skubber 1

TEST skubberReceiver != ST_RECEIVE1

AND skubberReceiver != ST_RECEIVE2

AND skubberReceiver != ST_RECEIVE3

AND skubberTime = 1

SET gotCase 0

TIMEOUT skubberTime ST_GOBACK

SETSTATE ST_GOBACK

ENDTEST

TEST skubberReceiver = ST_IDLE

SETSTATE ST_RESET

ENDTEST

END

State=ST_READY

SET skubber 0

SET motor 0

SET gotCase 1

TEST skubberReceiver = ST_EMPTY

TIMEOUT skubberTime ST_SEND

SETSTATE ST_SEND

ELSE

TEST foto = ST_FREE

SETSTATE ST_EMPTY

ENDTEST

ENDTEST

TEST parent = ST_IDLE

AND motorStopTime = 1

SETSTATE ST_IDLE

ENDTEST

END

### 708KasseInLiner.statemachine

STATEMACHINEVERSION 3

Include=cpkasseinliner.statemachine

Name=KasseInLiner

Link=prevback KasseInLiner

Link=prevleft KasseLoader

Link=prevright KasseInLiner

;** User Section **

STATEMACHINEVERSION 3

Name=KasseInLiner

;** Input **

;** Output **

Output=Motor "KasseInLiner Motor"

;** Link **

Link=prevback KasseInLinerPrevBack

Link=prevleft KasseInLinerPrevLeft

Link=prevright KasseInLinerPrevRight

Link=CamGen CamGenLift

Link=parent Parent

Link=KasseLift

Link=Foto KasseInLinerFoto

;** linkValue **

linkValue=Fototest test Foto

linkValue=loadfromleft Program

linkValue=loadfromright Program

linkValue=noShakeOnLast Program

;** Table **

;** Item **

;** Const **

Const=speedSend 0

Const=useMaxReceive 1

;** Value **

Value=errorCode 0

Value=simulate 0

linkValue=manuelt Program

;** Timeout **

Timeout=TimeStartUp 1000000

Timeout=TimeMaxSend 8000000

Timeout=TimeMaxReceive 8000000

Timeout=noShakeOnLastWaitSendTime 300000

State=ST_TIMER

END

State=ST_HALT

END

State=ST_IDLE

SET Motor 0

TEST parent = ST_RESET

AND manuelt = 0

SET errorCode 0

SETSTATE ST_RESET

ENDTEST

TEST simulate = 1

SETSTATE ST_RESET

ENDTEST

END

State=ST_RESET

TIMEOUT TimeStartUp ST_STARTUP

SETSTATE ST_STARTUP

END

State=ST_STARTUP

TEST TimeStartUp = 1

TEST Fototest = 0

SETSTATE ST_READY

ELSE

SETSTATE ST_EMPTY

ENDTEST

ENDTEST

END

State=ST_EMPTY

SET Motor 0

TEST loadfromleft = 1

AND prevleft = ST_SEND

TIMEOUT TimeMaxReceive ST_RECEIVE1

SETSTATE ST_RECEIVE1

ELSE

TEST loadfromright = 1

AND prevright = ST_SEND

TIMEOUT TimeMaxReceive ST_RECEIVE2

SETSTATE ST_RECEIVE2

ELSE

TEST prevback = ST_SEND

TIMEOUT TimeMaxReceive ST_RECEIVE3

SETSTATE ST_RECEIVE3

ENDTEST

ENDTEST

ENDTEST

TEST parent = ST_IDLE

AND simulate = 0

SETSTATE ST_IDLE

ENDTEST

END

State=ST_RECEIVE1

TEST TimeMaxReceive = 1

SET errorCode 1006

SETSTATE ST_IDLE

ENDTEST

TEST Fototest = 0

SETSTATE ST_READY

ENDTEST

END

State=ST_RECEIVE2

TEST TimeMaxReceive = 1

SET errorCode 1006

SETSTATE ST_IDLE

ENDTEST

TEST Fototest = 0

SETSTATE ST_READY

ENDTEST

END

State=ST_RECEIVE3

SET Motor 1

TEST TimeMaxReceive = 1

AND useMaxReceive = 1

SET errorCode 1006

SETSTATE ST_IDLE

ENDTEST

TEST Fototest = 0

SETSTATE ST_READY

ENDTEST

TEST parent = ST_IDLE

AND simulate = 0

AND useMaxReceive = 0

SETSTATE ST_IDLE

ENDTEST

END

State=ST_READY

SET Motor 0

TEST Fototest = 1

SETSTATE ST_EMPTY

ELSE

TEST KasseLift = ST_EMPTY

TIMEOUT TimeMaxSend ST_SEND

SETSTATE ST_SEND

ELSE

TEST noShakeOnLast = 1

AND speedSend = 1

TEST KasseLift = ST_SEND

TIMEOUT noShakeOnLastWaitSendTime ST_WAIT_SEND

SETSTATE ST_WAIT_SEND

ENDTEST

ENDTEST

ENDTEST

ENDTEST

TEST parent = ST_IDLE

AND simulate = 0

SETSTATE ST_IDLE

ENDTEST

END

State=ST_WAIT_SEND

TEST noShakeOnLastWaitSendTime = 1

TIMEOUT TimeMaxSend ST_SEND

SETSTATE ST_SEND

ENDTEST

END

State=ST_SEND

TEST KasseLift = ST_SEND

TEST noShakeOnLast = 1

SET Motor 1

ENDTEST

ELSE

TEST KasseLift = ST_RECEIVE

SET Motor 1

ELSE

SET Motor 0

ENDTEST

ENDTEST

TEST KasseLift != ST_RECEIVE

AND Fototest = 1

SETSTATE ST_EMPTY

ENDTEST

TEST TimeMaxSend = 1

SET errorCode 1012

SETSTATE ST_IDLE

ENDTEST

END

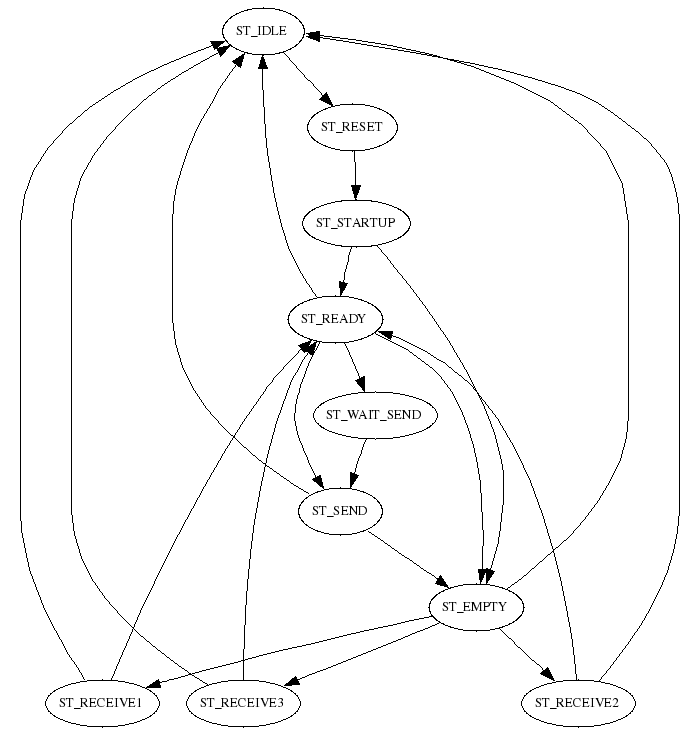
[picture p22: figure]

fig 24: 708KasseInLiner.statemachine

### 708KasseInLinerFoto.statemachine

STATEMACHINEVERSION 3

Include=input.statemachine

Name=KasseInLinerFoto

Input=input "KasseInLiner Foto"

Timeout=TimeOn 1000000

Timeout=TimeOff 700000

Value=test 0

Link=parent Parent

### 708Vibrator.statemachine

STATEMACHINEVERSION 3

Include=cpvibrator.statemachine

Name=Vibrator

;** User section **

STATEMACHINEVERSION 3

Name=Vibrator

Output=Vibrator "KasseLift Vibrator"

Link=KasseLift

Link=parent Parent

linkValue=vibrateTime Program

Timeout=TimeVibrate 20000000

State=ST_TIMER

END

State=ST_HALT

END

State=ST_IDLE

SET Vibrator 0

TEST parent = ST_RESET

SETSTATE ST_RESET

ENDTEST

END

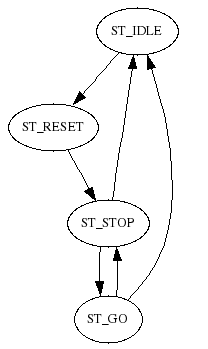
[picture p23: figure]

fig 25: 708Vibrator.statemachine

State=ST_RESET

SET TimeVibrate vibrateTime

SET Vibrator 0

SETSTATE ST_STOP

END

State=ST_STOP

SET Vibrator 0

TEST KasseLift = ST_SHAKE1

TIMEOUT TimeVibrate ST_GO

SETSTATE ST_GO

ENDTEST

TEST parent = ST_IDLE

SETSTATE ST_IDLE

ENDTEST

END

State=ST_GO

SET Vibrator 1

TEST TimeVibrate = 1

OR KasseLift = ST_SEND

SETSTATE ST_STOP

ENDTEST

TEST parent = ST_IDLE

SETSTATE ST_IDLE

ENDTEST

END

708

;*********************************

;* COMMON *

;*********************************

ITEM D9.item

ITEM C11.item

ITEM C14.item

ITEM C18.item

ITEM HSdoubleD9Cardboard.item

CPPATTERN Harndrup.cppattern

CPPATTERN DobbeltD9.cppattern

CPPATTERN C11Small8.cppattern

STATETEKST danish.statetekst

STATETEKST english.statetekst

STATETEKST spanish.statetekst

LANGUAGE danish.language

LANGUAGE english.language

LANGUAGE spanish.language

;*********************************

;* CP6000 V4 *

;*********************************

DIO 708.io

COMSK 708.comsk

MAC 708Skub.mac

MAC 708Buffer.mac

MAC 708Lift.mac

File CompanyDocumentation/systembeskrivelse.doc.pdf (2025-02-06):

Lukasz Zymla | MPN | Internship Report

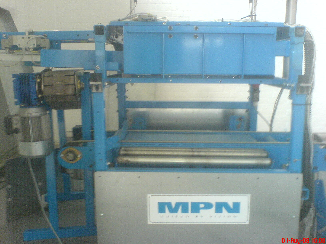
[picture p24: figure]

8

### 2. Case packaging machine CP4800

2.1.Introduction

CP4800 is a case packaging machine, which is putting products into cases. Originally it is a part of the system designed for Harndrup Frugtlager A/S. CP4800 together with CS1200 palletizing robot is a complete end-of-line packaging solution. Robot and case packer have common steering system. My task was to make CP4800 standalone machine.

2.2.Machine description

CP4800 with CS1200 is a complete solution for packaging fixed size trays, punnets or bags with products (for example tomatoes or onions). Trays are coming into CP4800, where two layers of eight products are put into plastic box (600x400mm). Filled box is coming out from the machine and is palletized by the CS1200 robot. Case packer is feed with empty boxes by the same robot, which is taking them from pallet with empty boxes (depalletizing).

Fig. 1 Case Packer CP4800
CP4800 is a simple machine. Trays, after leaving flow packer, are coming on narrow conveyor very close to each other. Just before CP4800 there is short “acceleration conveyor”, which is running faster – to make spaces between products. Trays are stopping on the mechanical stop and from the pushing place are pushed inside the machine. Two trays are pushed inside at one time. Two photosensors are

Lukasz Zymla | MPN | Internship Report

9

mounted on the pushing place to sense ready to push products. When the trays are being pushed, another are stopped by the side of the pusher, to avoid them from entering the pushing place. About 70 products can come into machine per minute. Inside the machine trays are placed on two metal plates. After pushing 4 times, 8 products are inside. Metal frame inside is pushing trays to the sides to put them close to each other. In the next step metal plates are opening to the sides, and products are falling down to the box below. They are also pushed from the top of CP4800, to avoid them from stocking on the way down. Box is going very fast up and down to create shake effect – trays should stay exactly on the bottom of the box, not on top of each other, to be ready for the next layer. Metal plates are closed immediately after products felt down, so the pusher can put new products inside almost without brakes. After putting two layers, filled box is going out from the machine and new one is pushed inside. To better imagine the whole process please visit company’s website¹

2.3.Steering system

### 2.3.1. Panel PC

As standalone machine case packer had to be separated from the robot cabinet. I was obligate to use panel PC as a control system. All MPN’s machine are running from panel PC’s with touchscreens and they have similar user interface. It means that panel PC is at the same time HMI (Human-Machine Interface) and main control system. Choosing Panel PC I didn’t have to write software from the beginning, but just make suitable changes. It also gives possibility to create friendly user interface. Bad thing about Industrial PC’s it that, they doesn’t have any inputs/outputs. By saying input/output I mean mainly single digital signals from sensors (like photo or temperature sensors) and to actuators (like air cylinders), not PC’s communication port like Ethernet or USB port, which obviously most of the PC’s have. Case packer CP4800 is steered by air – it requires lot’s of inputs and outputs for air cylinders. Best choice for managing inputs/outputs is PLC. If we want to extend functionality of our PC we must buy modules usually produced by other companies. With PLC we can get all modules from one manufacturer and don’t have to worry about communication or power supply for the modules. PLC’s extension modules from the same product line have usually standardized sizes so it is easier to mount them in electrical cabinet.
In the first robots MPN was using PLC’s for managing inputs and outputs. To communicate with PC, PLC had some inputs/outputs connected to I/O’s of motion controller. Trio Motion Controller is able to communicate with PC via Ethernet. So PC was communicating with PLC not directly. This was complicated and not efficient way to

1
http://www.mpnrobotics.com/en/20/products/cp4800.html?area=movie

Lukasz Zymla | MPN | Internship Report


10

manage inputs and outputs. It require to write 3 programs: for PC, motion controller and PLC. Later on MPN’s choice was Telemecanique Advantys.

### 2.3.2. Advantys

Advantys STB²
is a distributed I/O platform. The whole segment is called Island. Main module in the island is Network Communication Module. After NIM we can easily connect many different functional modules: digital and analog input/output modules, power distribution modules, motor control modules and other specialized modules. What is interesting about this system that we are allowed to change failed I/O modules without shutting down the machine.
Fig. 2 Advantys STB Island | Fig. 3 SMC Manifold

I have used Advantys, because there is written driver for communication with MPN's software. I had to build my own island. Some of the modules were on stock, the rest was ordered. CP4800 requires 23 digital inputs, 16 outputs and 3 motors. My island consists of 8 modules:
- 1x NIP 212 – Ethernet communication module
- 1x PDT 3100 - power supply module for inputs and outputs
- 4x DDI 3610 – 6 digital inputs module
- 1x DDO 3705 – 16 digital outputs module
- 1x EPI 2145 – up to 4 motors can be connected Additionally is needed mounting terminal for each module, termination for Island end, connectors for wiring input and outputs and Tesys motor drives

2
http://www.us.telemecanique.com/products/automation/Distributed_IO/Advantys_STB/index.html

Lukasz Zymla | MPN | Internship Report


11

Fig. 4 Wired Advantys Island for CP4800 with connected via Ethernet cable Tesys motor drives

It is possible to use cross-over Ethernet cable to connect Advantys directly to panel PC or use straight cables with Ethernet switch between.

### 2.3.3. Air cylinders

CP4800 uses a lot of pneumatic cylinders as linear actuators. They are controlled by valves and manifolds manufactured by SMC which are connected to Advantys output modules. Some of air cylinders has position sensors which are sending signals to Advantsys’ digital inputs. Air cylinders have only 2 possible positions – with stroke inside and outside. It is one of the reason why CP4800 is working with only one type of boxes. In CP6000 box lift is controlled by servo, so box position (height) can be perfectly adjusted. With air cylinders it is also not possible to control speed and acceleration of motion very accurate – only by regulating air pressure. But they are cheaper than electric actuators and they are good enough for this solution. Air cylinders have different lengths.
Idea for the future is to use SMC Serial Interface Units ex250 or ex500. This solution is eliminating Advantys I/O’s. Those units can communicate with panel PC via Ethernet/IP open source protocol. They require also less wiring.

### 2.3.4. Motors

CP4800 has 3 motors: one inside the machine for conveyor transporting out filled boxes and two products transporting conveyors. All of them are 3 phases 400 VAC. They are controlled from Advantys EPI 2145 module. This module is connected to Tesys drives via Ethernet cables. Tesys is responsible for giving power to motors and protect them from trip. Tesys consists of modules which can be built like Lego. We can choose modules with different adjustable maximum output current – depending on our motor

Lukasz Zymla | MPN | Internship Report

12

specification. It is possible also to run motor in two directions with Tesys – but this is not required for CP4800. If motor is tripped, adequate message is showed on panel PC.

### 2.3.5. Photosensors

Case Packer has 3 Omron photosensors. Omron is producing wide range of photosensors with different parameters like working distance or PNP - NPN.

### 2.3.6. Safety and interface

During steering design we cannot forget about safety issues and interface. One of the most important buttons on every machine is emergency stop. This button should cut all power to outputs when pressed. It should stop motors and all actuators.
Another common thing for industrial machines are traffic lights. They can in a simple way show operator in which state machine is: emergency stop pressed, pause, error or running. Traffic lights should be mounted on top of the machine, that operator can easily see them from distance and react if necessary
Industrial environment is not friendly for the machine. In case packer vegetables and fruits can be smashed and damage steering system. All the devices are made for industry, so they should be resistant for those kind of situation. But even dough industrial PC is designed to work in dusty environment it should be mounted properly. Some of mounting cabinets has special exchangeable filters, which protects from dust and allow air circulation. It is important not to overheat devices inside cabinets.
We cannot forget about power switch for the machine, eliminating unplugging the power cable when it is necessary to turn off the machine.

2.4.Software

### 2.4.1. Linux

MPN's software is based on Linux environment. They are using Fedora Core 6 for programming. I hadn't got many experiences with Linux operating system before. During internship period I have learned basics of Linux, especially use of terminal.
Main program, which is running on MPN's machines, is written mostly in C and C++. This application is called Robostacker. It is able to control all MPN's machines: robots, case packers, checkweighers, pallet and case magazines. Robostacker is running on the machine’s panel PC's from Flash card. Flash cards are easy to exchange, which can be used for software update of the machine. Each Flash card has 2 partitions: first one with small Linux (about 7MB), second with main program(few MB).

Lukasz Zymla | MPN | Internship Report

13

### 2.4.2. Robostacker

### 2.4.2.1. Introduction

Main idea of this application is to control all machines. Compiled program is copied to the machine. All machine details required by the program are loaded from database. If we want to makes changes in the machine’s programs, we just simply adjust database. This approach eliminates re-compiling of the Robostacker after each change.

### 2.4.2.2. Modbus - communication protocol

Robostacker is gathering information from external devices via Ethernet. Modbus TCP/IP³
protocol is responsible for handling communication. It belongs to fieldbus – family of real-time industrial computer networks protocols. Modbus TCP/IP provides a reliable data transport between devices. It is open protocol based on Modbus Protocol developed by Modicon in 1979. Protocol is working on standard Ethernet infrastructure, so we are allowed to use for example standard Ethernet switches. Many industrial devices from different vendors are Modbus compatible. All devices in the network have static IP. On the other hand use of Ethernet as a communication medium, gives possibilities of distributed management. It is possible to login into machine and make changes in software from other part of the Globe – machine just need Internet connection.
It is possible to test Robostacker program on normal PC. Because it needs connection to specified hardware, it has to be run in simulation mode. In that mode all external devices like Advantys or motion controllers are simulated by software. Machines can only be programmed off-line, but it is possible to adjust parameters on-line. Every time we need to change something in flow of the program, either we take out the flash and connect it to PC, either connecting to Panel PC via Ethernet. Remote connection is done by Linux – login to the machine – and mounting file system. Programmer can copy all required changes from his own PC.
Each device in the network requires driver. Drivers are written in C language and compiled with Robostacker. The reason that all devices need individual driver is that they need to talk with Robostacker. All devices has their individual set of messages, status, registers and errors sent using Modbus TCP/IP.

### 2.4.2.3. Database

During every machine boot-up Robostacker is reading important machine parameters from the set of text-files called ‘database’. Files are read line by line into memory. Most important catalogues in database are:

3
http://www.modbus.org/

Lukasz Zymla | MPN | Internship Report

14

- system – file system.ini contains information about machine details like: id, location, panel PC and Advantys IP address, touchscreen calibration values, access level, main interface dialog
- workcell – file *.workcell contains list of all other files from database which should be loaded during boot-up
- statemachine – files *.statemachine describe whole behavior of the machine. Each file is responsible for small piece of the robot. Company has developed their own language for writing statemachines. It has functionality like any other programming language: definition of variables and constants, logical operators, conditionals, etc. Every statemachine contains many states and can be in one state at a time. Every statemachine contains set of standard states like Halt, Idle, Reset, Timer, as well as set of individual states. During program execution statemachine is jumping between different states, depending on actual conditions. It can test on inputs like photo sensors or other statemachines. Programmer can define many statemachines. Sometimes statemachine is only responsible for controlling single sensor. Use of statemachines is very clever, cause it makes programming more similar to object-oriented. Each part of the machines is acting as independent object. I have taken all statemachines connected with case packer from old system in Harndrup. I had to write also few new statemachines to run CP4800 as independent machine.
- dio – file *.io contains information about Advantys, like island’s IP address, number and names of modules. It also links all inputs and outputs with their individual names, which are used in statemachines. I had to create *.io file corresponding to Advantys Island
- language – file *.language contains languagepack for GUI. It is possible to switch languages from menu
- statetekst – file *.statetekst contains machine status messages displayed on the screen. They are also in different languages
- item – file *.item describes properties (dimensions) of box in which products are being packaged.
- cppatern – file *.cppatern contains information about number of products and layers in the box

Lukasz Zymla | MPN | Internship Report


15

Fig. 5 Database

### 2.4.2.4. GUI

Big advantage of MPN’s machines is color touchscreen. It gives possibility to create advanced and dynamic Graphical User Interface.
Touchscreen size is 12”, so user interface shouldn’t be too complicated and contain too many information at one time. Buttons should be big enough to press it with finger. Sometimes workers are wearing gloves.
There are different access levels – some options are only available for supervisors or service. It provides necessary security and possibility of machine service using user interface.
Each MPN’s machine has similar user interface: colors, shape of buttons and their placement on the screen. It is easier to operate different machines in one factory for personnel. So it was very important to keep the existing GUI. There is possibility to change language, so machines are ready to be sold abroad.
Use of panel PC gives possibility to do even more advanced and user-friendly HMI. One of the idea are animations and simulations of machine behavior displayed on the screen.

### 2.4.3. Advantys

After building physical island it needs to be configured. With hardware there is delivered Advantys Configuration Software for Windows. Program is very simple and easy to use. You just need to build your Island by choosing elements from library and upload it. Small range of IP addresses is possible to choose using screw driver, but if we are already online we can set any address to memory. Whole Island configuration is stored in communication module.

Lukasz Zymla | MPN | Internship Report


16

Fig. 6 Advantys Configuration Software

### 2.4.4. Supporting program

For easier programming MPN has developed some supporting programs. One of them is mpnguide. MPN’s palletizing robots are programmed offline. Mpnguide is a program for graphical representation of programmed paths. In the program we can observe our paths and keep track of many parameters, like engines acceleration. It is very important to simulate them before testing on real robot.
My idea is to develop a program for graphical representation of statemachines. It is much easier to follow a flow of a program form a graph than from a plain text.
I made research on the Internet, because I couldn’t use any of the graphs that I learned on my previous course: object oriented system analysis and design. I read a little about state diagram used to graphically represent finite state machines and found OMAC state model (fig. 8). I have also tried to find software that can translate statemachine to a graph. My choice is Graphviz. It is open-source software, already installed in many Linux distribution. There is also Windows version. Graphviz is drawing graphs from text files. It is able to draw many types of graphs and user has big control over graphs: shapes, colors, comments on arrows.

Lukasz Zymla | MPN | Internship Report


17

Fig. 7 Statemachine graph from Graphviz | Fig. 8 OMAC state model

Idea of my program, that I called mpngraph, is to translate statemachine code into code interpretable by Graphviz. Than mpngraph should run Graphviz, which will save graph in preferable file type for printing or viewing on the screen. Graphviz supports many file types from gif and jpg to pdf. It is possible to run Graphviz from terminal.
Some code could be taken from Robostacker, cause it is already able to read each statemachine line by line. After reading each line, mpngraph should interpret it and generate suitable code for Graphviz. Mpngraph could be run from terminal or have simple GUI. Some of the statemachines are very long, so user should choose which information would he like on the graph. The most simple idea is just to show states and arrows from them to the states that are possible to jump to. Other information could be condition of state change written on arrow or inputs and outputs used in this state. Program could be also use for machine testing, to highlight on panel PC current state.

### 2.5. Test

I have tested CP4800 with palletizing robot. I needed two signals between machines:
- Case packer is ready to receive empty box
- Robot is ready to receive full box for palletizing
Machines were working without any problems.

2.6.Conclusion
- CP4800 is able to work as standalone machine
- CP4800 is cheap, because it is steered by compressed air – without servo motors
- It is fast, simple and reliable
- It is not universal, because it is working with only one type of boxes

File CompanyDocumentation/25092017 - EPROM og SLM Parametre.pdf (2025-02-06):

## EPROM

Position | Navn i kode | Navn i dokumentation
0-7 | ctcoder parameters | ???
0-18 | Værdier til udregning af Encoder Objekt checksum (akse specifik) | ???
19 Værdi til sammenligning med udregnet Encoder | Objekt checksum (akse specifik) | ???
20 Værdi til sammenligning med udregnet Motor | Objekt checksum (akse specifik) | ???
21 | Antallet af instances i Motor Objekt | ???
22 | Encoder data version | ???
29 | Flux alignment position | ???
30 | Motor current | ???
31 | Poles (antallet af poler i motoren) | ???
32 | Winding time constant | ???
37 | Motor RPM | ???
21-47 | Værdier til udregning af Motor Objekt checksum (akse specifik) (antallet af instances bliver også brugt i denne udregning) | ???
50 Værdi til sammenligning med udregnet checksum | for Performance Objekt | ???
51 | Antallet af instances i Performance Objekt | ???
52 | Performance Objekt version | ???
53 | Motor kp-værdi (Proportional-del i PID regulering) | ???
54 | Motor ki-værdi (Integral-del i PID regulering) | ???
55 | Motor kd-værdi (Differential-del i PID regulering) | ???
56 | Current scaling (strøm skalering) | ???
57 | Speed loop filter cut off frequency | ???
51-90 | Værdier til udregning af Performance Objekt checksum (akse specifik) (antallet af instances bliver også brugt i denne udregning) | ???

## SLM Parametre

Position | Navn i kode | Navn i dokumentation
1 | a=(((kp/ki)+kd)*4*ss)/ts (akse specifik) | ???
2 | b=ki*32768*ts/kp (akse specifik) | ???
3 | c=ki*64*ss (akse specifik) | ???
4 | d=(kp*ss)/ts (akse specifik) | ???
5 | e=d*65535/(d+ki) (akse specifik) | ???
6 | f=digit_limit/((ki+(kp/ts))*ss) (akse specifik) | ???
7 | Current scale/strøm skalering (akse specifik) | ???
8 | Poles/antallet af poler (akse specifik) | ???
9 | p9=65535-(current_scale*0.25/16) (akse specifik) | ???
10 | p10=65535-(current_scale*0.25) (akse specifik) | ???
11 absolute speed maximum trip threashold (akse | specifik) | ???
12 | MultiAx Read Address (akse specifik) | ???
13 | speed loop filter cut off frequency (akse specifik) | ???
14 | phase advance (akse specifik) | ???
15 | flux alignment position (akse specifik) | ???
16-23 | CT-Coder parametre (akse specifik) | ???
28 | CT-Coder status (akse specifik) | ???
29 | winding time constant (akse specifik) | ???
35 | I2t backoff level (akse specifik) | ???
36 | p36=(((32*motor_current*129)/ (drive_current*100))^2) (akse specifik) ved ikke hvad det er. | ???
37 | hysteresis (akse specifik) | ???
39 | ??? Noger med om det er high-speed motor | ???
62 | Host flag (akse specifik) | ???
74 | Position (akse specifik) | ???
75 | Flux (akse specifik) | ???
76 | Zero ?nulpunkt? (akse specifik) | ???
90 | Rev ?aktuelle rpm/omdrejninger? (akse specifik) | ???

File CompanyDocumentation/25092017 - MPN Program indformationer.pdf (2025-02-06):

## MPN Program indformationer

- RoboStacker software
- For at starte robostacker software skal man via terminalen i linux navigere til rs-mappen i udviklingsmappen som regel kaldet testbox eller sandbox og bruge kommandoen ./robostacker for at starte programmet med de informationer der i mntdatabase.txt i rs-mappen.
- Vil man starte robostacker software op som simulation skal man tilføje -s efter ./robostacker : ./robostacker -s
- Skrives der -s mouse kan robostacker startes som det vil kører på en pallePC, men med klik og bevægelse i GUI styret fra musen i stedet for via touch-skærm på pallePC.
- Med argumentet -w er det muligt at starte robostacker software op med et andet workcell-ID end det der står i mntdatabase.txt, men med samme database fx ville ./robostacker -w 325 starte robostacker software op med 325system.ini i stedet for 329system.ini som stod i mntdatabase.txt, men stadig bruge ../../mnt/database/ som stien til hvor filerne skal findes.
- -db bruges til at indikere at der skal bruges en database fra en anden filsti, hvis man vil bruge en anden database med ændringer eller nyere information kombineres -w og -db og bliver til ./robostacker -w 329 -db ../../sandbox/mnt/database/.
- MPNGUIDE
- Program til at hjælpe med at lave paths til robotten, startes ved at gå ind i projekt-mappe og derefter ind i mpnguide og ind i mpnguide igen i linux terminal og skrive ./mpnguide

mntdatabase.txt
../../mnt/database/
329system.ini

- For at ændre hvilken opstilling der startes mpnguide for skal der ændre i mntdatabase.txt her er der sti til database og på linjen efter en WIDsystem.ini som henviser til hvilken opstilling der skal startes op fx:
- Statemachines:
- System.ini konfigurations-fil, indeholder workcell-id, lokation, IP-adresse på pallePC, IP-adresse på Motion Coordinator, touch-skærm opsætning, GUI form m.m.
- Workcell-ID.workcell indeholder liste over navne på alle de filer der skal bruges til den pågældende opstilling.
- ITEM-filer er beskrivelser af standard ting der bliver brugt som europaller eller C18-kasser og tilhørende kassemagasiner. Størrelses dimensioner og vægt.
- STATETEKST-filer er filer der indeholder GUI-tekst på forskellige sprog, der gør det muligt at skifte sprog på GUI.
- LANGUAGE-filer ligesom STATETEKST-filer
- ROBOT-filI indeholder beskrivelse og dimensioner af robotten, længde af gantry, højde på gantryben, skuldergear i robotten, ratings af Nm på gear og motor, RPM for gear og motor, gearing, enheder, PID værdier, hastighed, acceleration, decelleration, krypehastighed, JOG-hastighed og frame-definitioner på home-position, palle placering og conveyerbælter.
- TOOL-fil indeholder dimensioner af vætktøjet som robotten bruger, vægt og antal ting der bliver løftet ad gangen.
- ACCESSORY-filerindeholder beskrivelse og dimensioner på tilbehør til robotten som fx bæltebaner.
- DIO-fil indeholder IP-adresse på advansysmodul, antallet af IO moduler i advansys og koder for forskellige slags moduler og navne på IO til brug i STATEMACHINES.
- ****.STATEMACHINE disse filer udgører opstillingens funktion, disse filer fortolkes af Robostacker software og får maskinopstillingen til at køre.
- Er en robot linket sammen med en anden på netværk vil komunikation med denne foregå i remotevalues.statemachine
- REMOTEHOST – IP-adresse på en eventuel anden robot/maskine som der skal kommunikeres med.

mntdatabase.txt
../../mnt/database/
329system.ini

- BOPRCOEFF-fil denne fil indeholder koeficienter der skal bruges i forbindelse med specielle paths robotten skal tage for at undgå ting i arbejdsområdet.
- Workcell ID numre og deres betydning
- 300-serie: Robostacker CS1200/RS2050
- 400-serie: Robostacker RS2050
- 500-serie: CheckWeigher
- 700-serie: CP6000, kassepakker
- 800-serie: Kasse magasin
- TRIO programmer styrer HAC, SAC, motorer osv.
- ZPOWERUP.bas initialiserer TRIO, HAC, SAC, encoderer og motorer. Tjekker og giver fejlmeddelelser på motor, encoder og current-trips. Akserne på robotten bliver initialiseret med værdier for bl.a. motorstrøm, PID regulering, acceleration og decelleration. Kører de forskellige paths ud fra værdier i VR-array.
- ZCTLCOMMAND.bas er jeg endu ikke helt sikker på, men der er statemachine der styrer lystræ/lyssignal med rød/gul/grøn lampe.
- ZMPNSCOPE.bas jeg har ikke umiddelbart nogen ide om hvad den gør på nuværende tidspunkt.
- TESTSLM.bas laver test af forbindelse til motor og encoder
- SLMSTATUS.bas er et status program der holder øje med status på SLM-kort og giver besked om hvad status er i øjeblikket
- Hvis TRIO går i fejl under opstart, så log på med Motion Perfect 2 og tryk på Scan for intelligent devices hvis den ikke finder det ene board er det pågældende SLM kort nok defekt. (Det er ikke sikker et DrivelinK [COM0007] board kan udskiftes med et SLM Technologies [COM0008], men måske det SLM Technologies board jeg havde fat i også var defekt). Ligesom med slm boards og version tror jeg det kan være med version på encoder.
- Robostacker software snakker med TRIO'en gennem en GLOBAL tabel kaldet VR, som har 1024 variabler (0-1023)
- VR(0)-(9) bliver brugt til zmpnscope task i TRIO'en
- VR(10)-(99) bliver brugt til forskellige robot paths
- VR(800)-(899) bliver brugt til globale variabler, blandt andet definition af placering af HAC og SAC på SLM slots og motor placeringer på HAC og SAC
- VR(1000)-(1023) bliver brugt til home positioner, workcell-type, workcell-id m.m
- Robottens path mellem forskellige positioner er programmeret i TRIO'en, ændringer i positionskoordinater bliver kommunikeret til TRIO'en via Modbus til VR-tabel.

- I TRIO'en når der skal laves forbindelse akserne forbundet til HAC og SAC, vil disse altid være SLM-kort i SLOT 1 og 2, data Ethernet/Modbus altid skal være i SLOT 0. Axis A på en MultiAx er på ASIC 0, Axis B på en MultiAx er på ASIC 1 og Axis C på en MultiAx er på ASIC 2.
- Mihada robotten (nr 307/328) har ikke aktiveret E-aksen, men der er stadig motor på robotten og motoren er forbundet. Jeg ved ikke om E-aksen har været brugt tidligere eller om den bare aldrig har været taget fra, men hvis den ikke bliver brugt forstår jeg ikke helt hvorfor den sidder på og er forbundet til strøm.

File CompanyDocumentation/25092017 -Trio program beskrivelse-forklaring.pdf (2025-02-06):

# Trio program beskrivelse/forklaring

ZPOWERUP.bas

ETHERNET(2,0,7,1)
ETHERNET(2,0,9,1)
…
Disse to linjer er til opsætning af kommunikation over ethernet via Modbus/TCP.
1. Første linje definerer hvilken datatype der skal bruges i kommunikationen, 2 og 7 er faste argumenter ved denne definition, 0 er hvilket slot i TRIO'en ethernet-daughter board sidder på og 1 betyder at der er valgt 32bit signed floating point (havde der været 0 i stedet for 1, havde der været valgt 16bit signed integer, dette er også standard
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

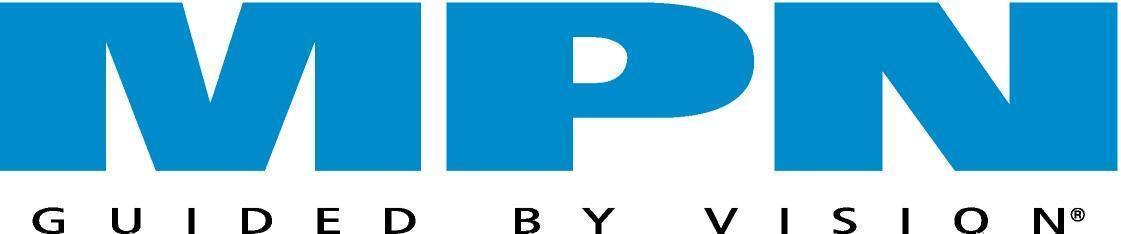
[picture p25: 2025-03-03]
CaddyDXF/newDrawings/Servo_kassepakker/Langbufferskub - 0023 - Kredsskema - 0023 - Image1.bmp

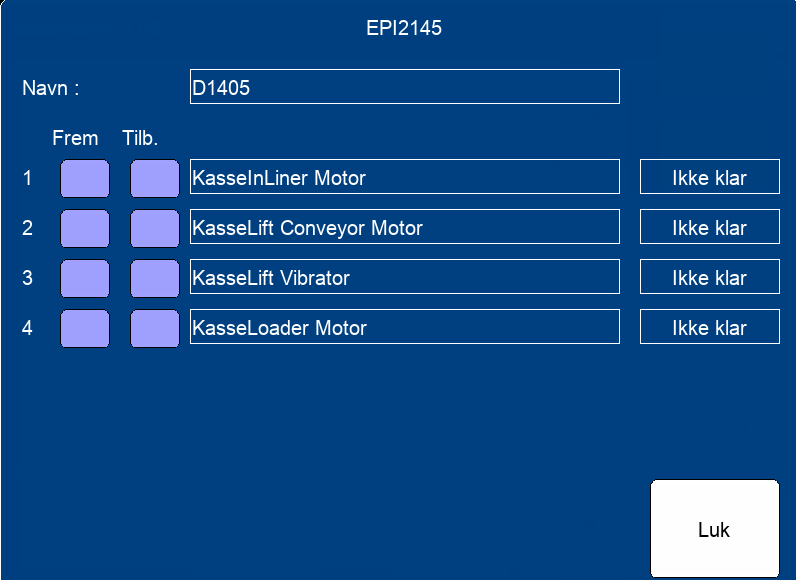
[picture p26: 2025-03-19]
Advantys input output/EPI2145 D1405.png

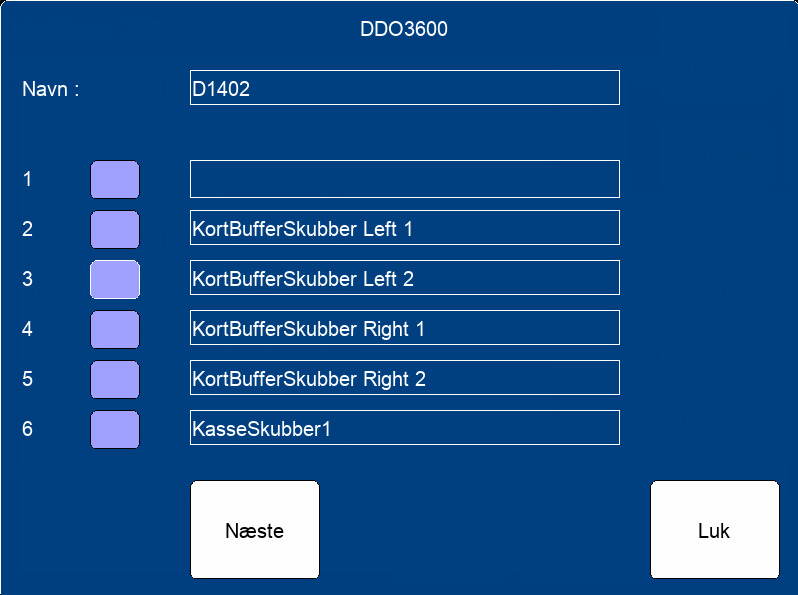
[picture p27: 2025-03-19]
Advantys input output/DDO 1402.png

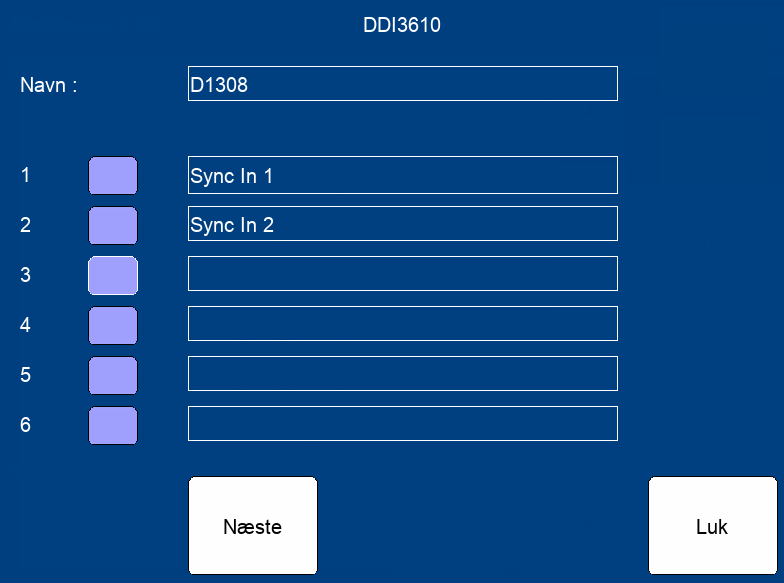
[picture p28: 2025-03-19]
Advantys input output/DDI 1308.png

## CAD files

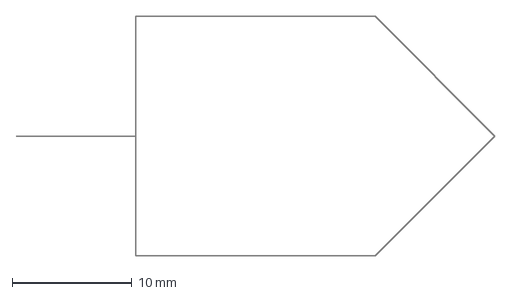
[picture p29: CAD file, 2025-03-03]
CaddyDXF/DFXComponentsLibrary/DigitalComponents/output.dxf
40.0 x 20.0 mm

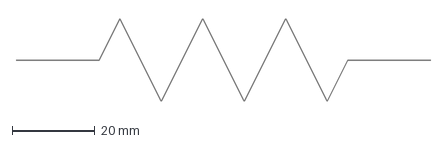
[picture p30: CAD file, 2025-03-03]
CaddyDXF/DFXComponentsLibrary/ElectronicComponents/resistor.dxf
100.0 x 20.0 mm

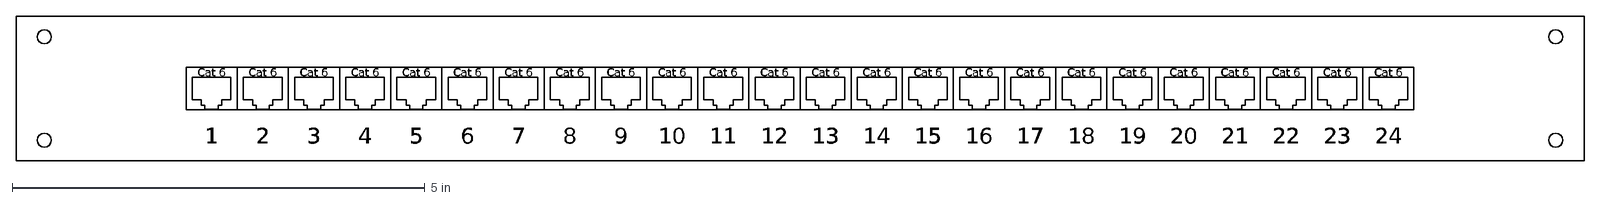
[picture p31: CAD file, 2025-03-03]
CaddyDXF/DFXComponentsLibrary/NetworkComponents/Equipment/Network/PatchPanel24Port.dxf
1
2
3
4
5
6
7
8
Cat 6
9
10
11
12
13
14
15
16
17
18
19
20
21
22
23
24

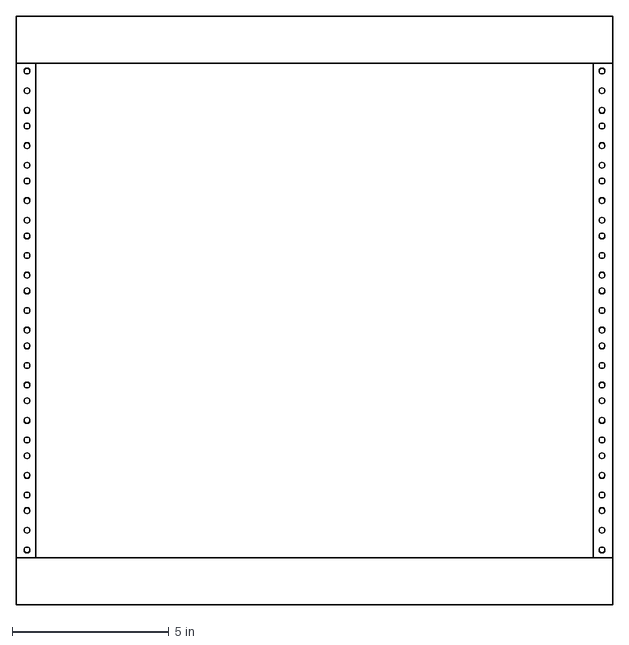
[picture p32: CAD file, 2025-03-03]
CaddyDXF/DFXComponentsLibrary/NetworkComponents/Equipment/Rack/19in9u.dxf
19.0 x 18.8 in

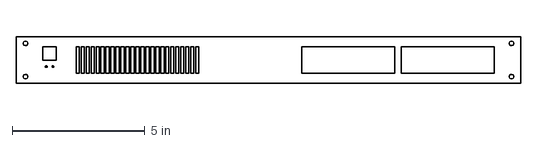
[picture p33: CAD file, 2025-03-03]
CaddyDXF/DFXComponentsLibrary/NetworkComponents/Equipment/Servers/Server1U.dxf
19.0 x 1.75 in

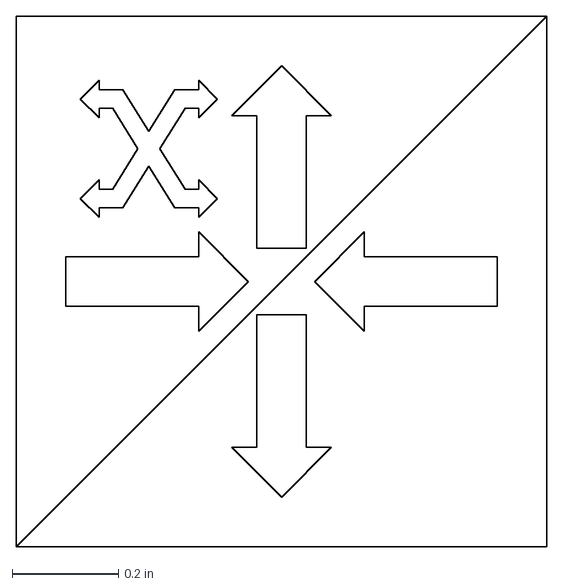
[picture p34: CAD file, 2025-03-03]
CaddyDXF/DFXComponentsLibrary/NetworkComponents/Logical/RouterFirewallSwitch.dxf
1.00 x 1.00 in

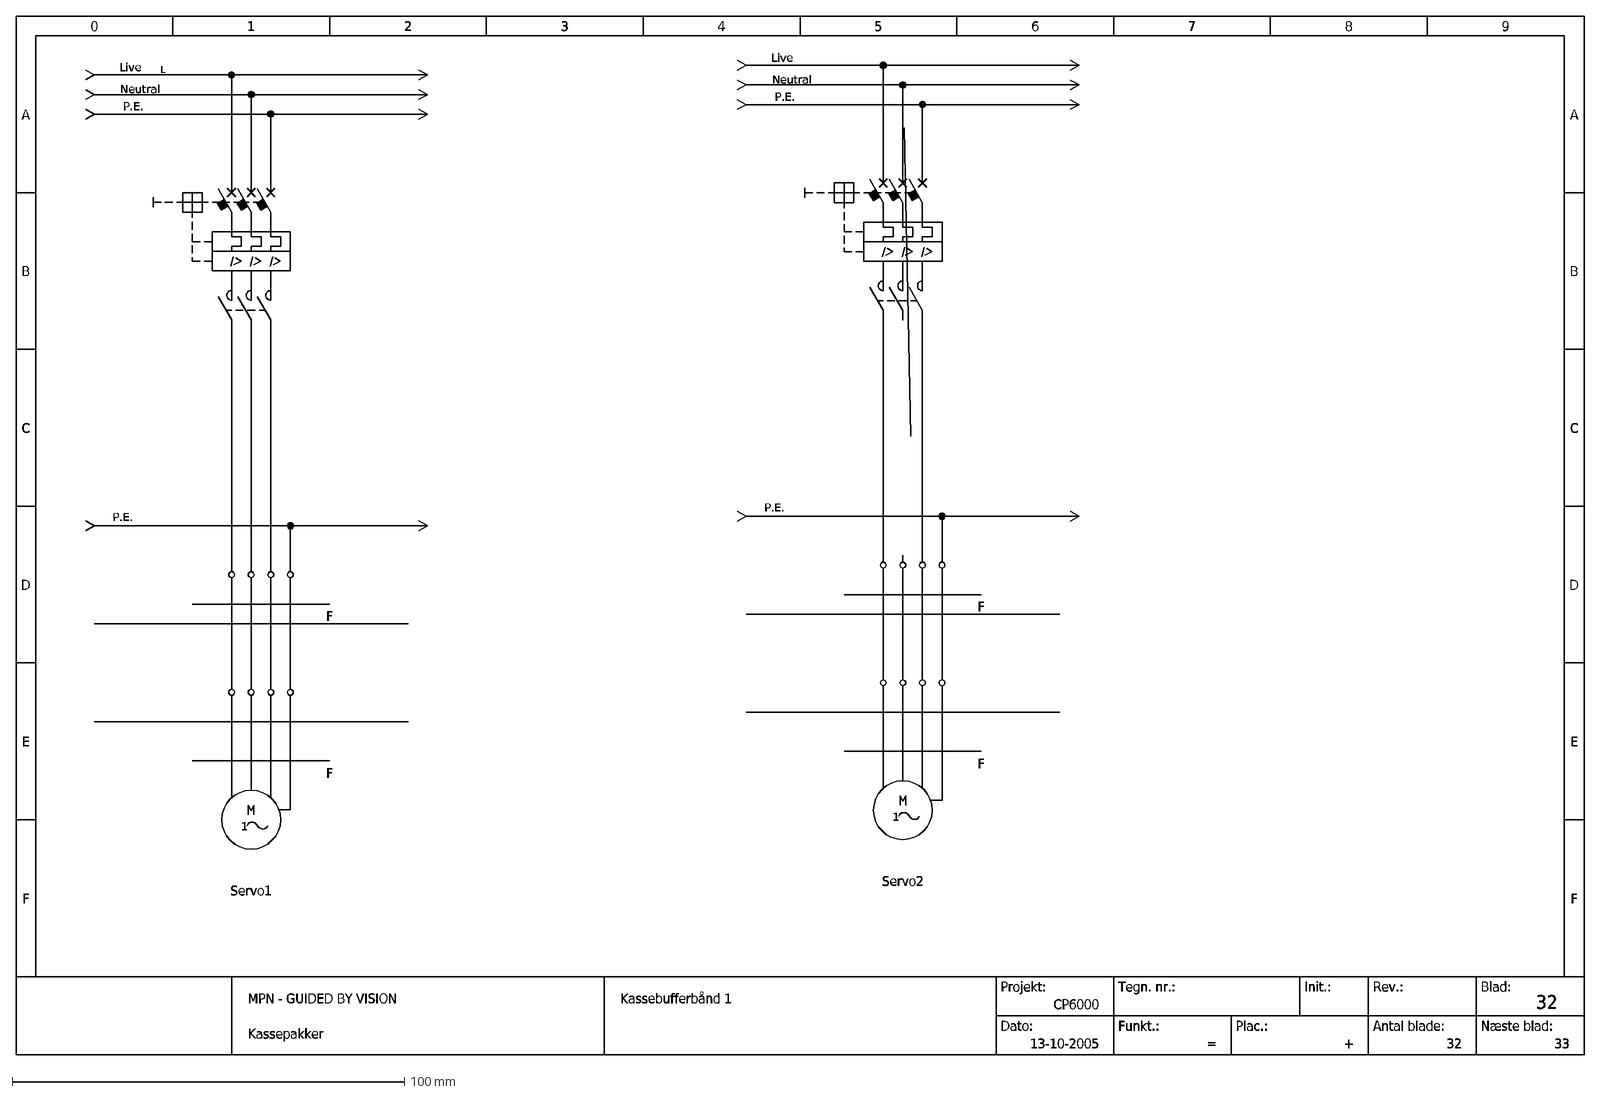
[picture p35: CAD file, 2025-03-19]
CaddyDXF/Kassebufferbånd1 - 0032.dxf
0
1
2
3
4
5
6
7
8
9
A
B
C
D
E
F
Kassepakker
MPN - GUIDED BY VISION
Kassebufferbånd 1
Projekt:
Dato:
Funkt.:
Tegn. nr.:
CP6000
13-10-2005
Plac.:
=
+
Rev.:
Init.:
32
Blad:
33
Næste blad:
Antal blade:
L
Live
Neutral
P.E.
Servo2
Servo1

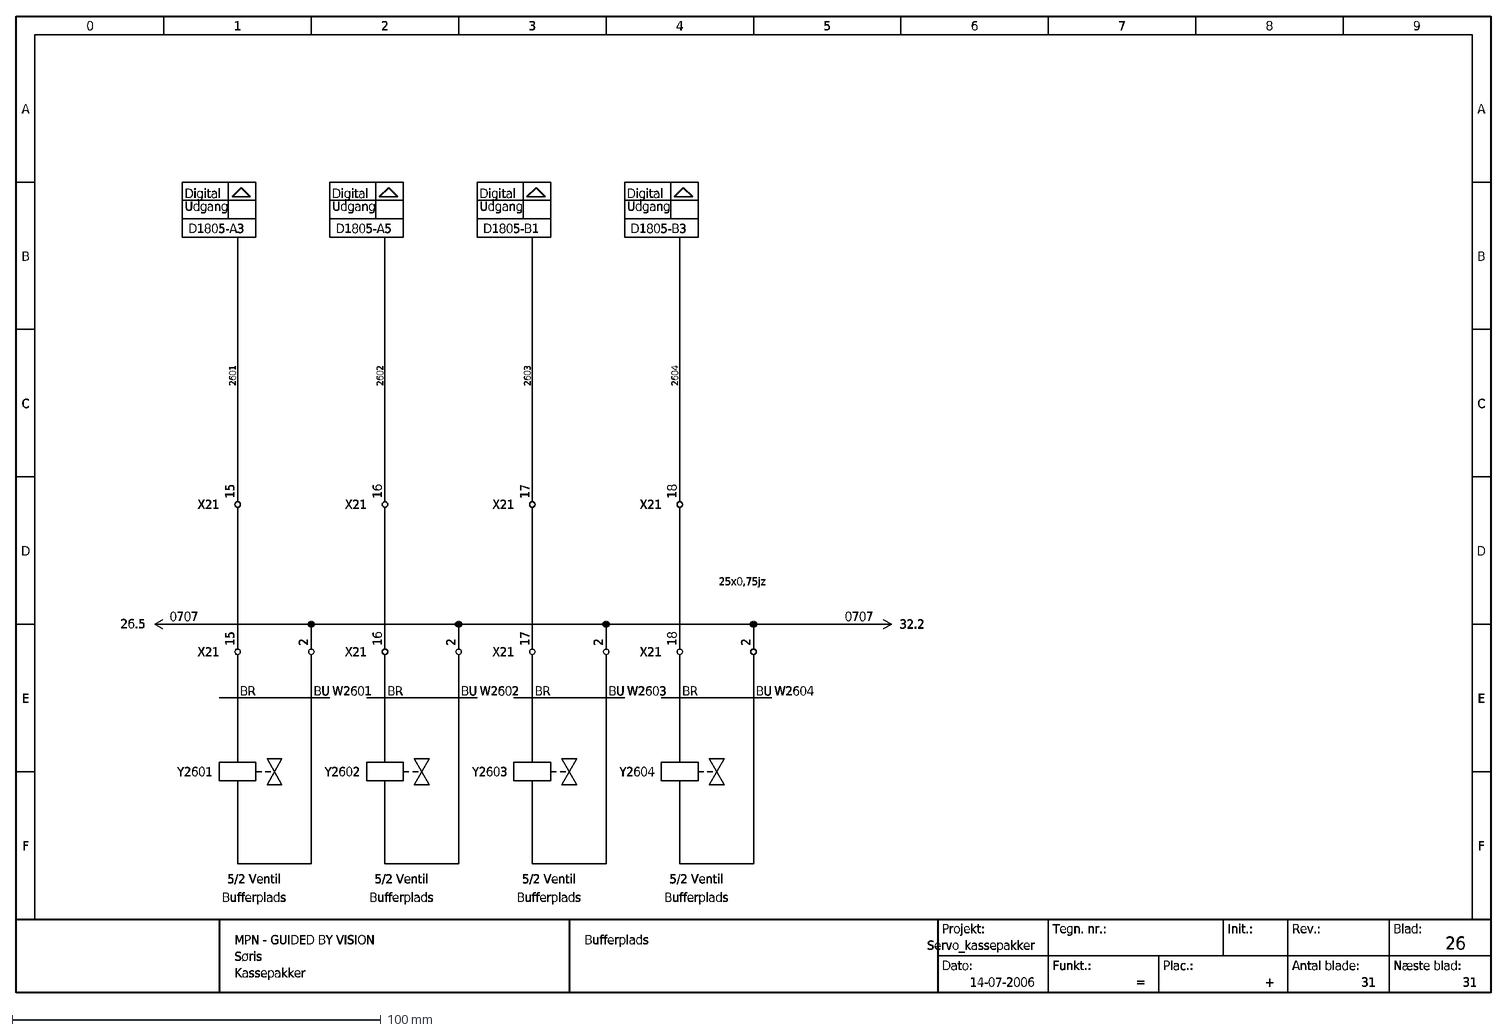
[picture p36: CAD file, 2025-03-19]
CaddyDXF/newDrawings/Servo_kassepakker/BufferpladsVentil - 0026.dxf
0
1
2
3
4
5
6
7
8
9
A
B
C
D
E
F
Kassepakker
MPN - GUIDED BY VISION
Søris
Bufferplads
Projekt:
Dato:
Funkt.:
Tegn. nr.:
Servo_kassepakker
14-07-2006
Plac.:
=
+
Rev.:
Init.:
26
Blad:
31
Næste blad:
Antal blade:
X21
15
1911763
AB1RR235U2GR
-X
1911764
Y2601
5/2 Ventil
D1805-A3
#00000033
Digital
Udgang
35
2601
16
Y2602
D1805-A5
2602
17
Y2603
D1805-B1
2603
18
Y2604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

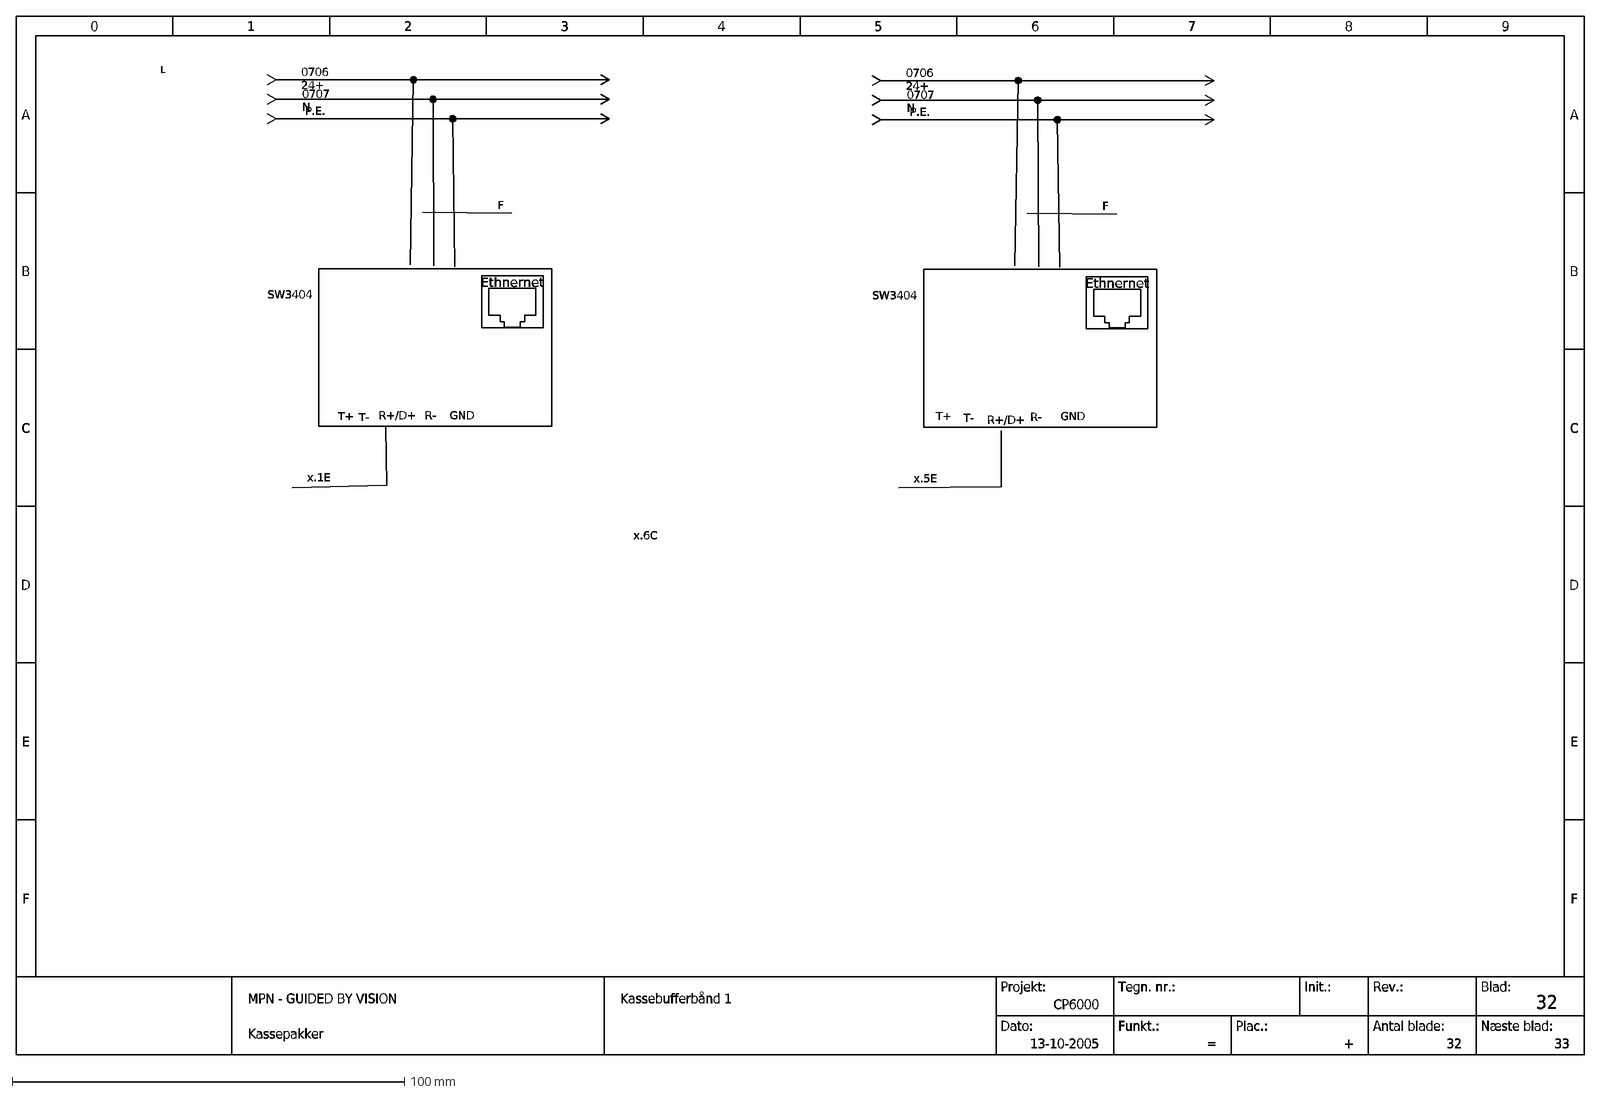
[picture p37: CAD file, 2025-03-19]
CaddyDXF/testDrawings/Kassebufferbånd1MOXA.dxf
0
1
2
3
4
5
6
7
8
9
A
B
C
D
E
F
Kassepakker
MPN - GUIDED BY VISION
Kassebufferbånd 1
Projekt:
Dato:
Funkt.:
Tegn. nr.:
CP6000
13-10-2005
Plac.:
=
+
Rev.:
Init.:
32
Blad:
33
Næste blad:
Antal blade:
L
P.E.
SW3404
Ethnernet
0707 N
0706 24+
T-
T+
x.1E
R-
GND
R+/D+
x.5E
x.6C

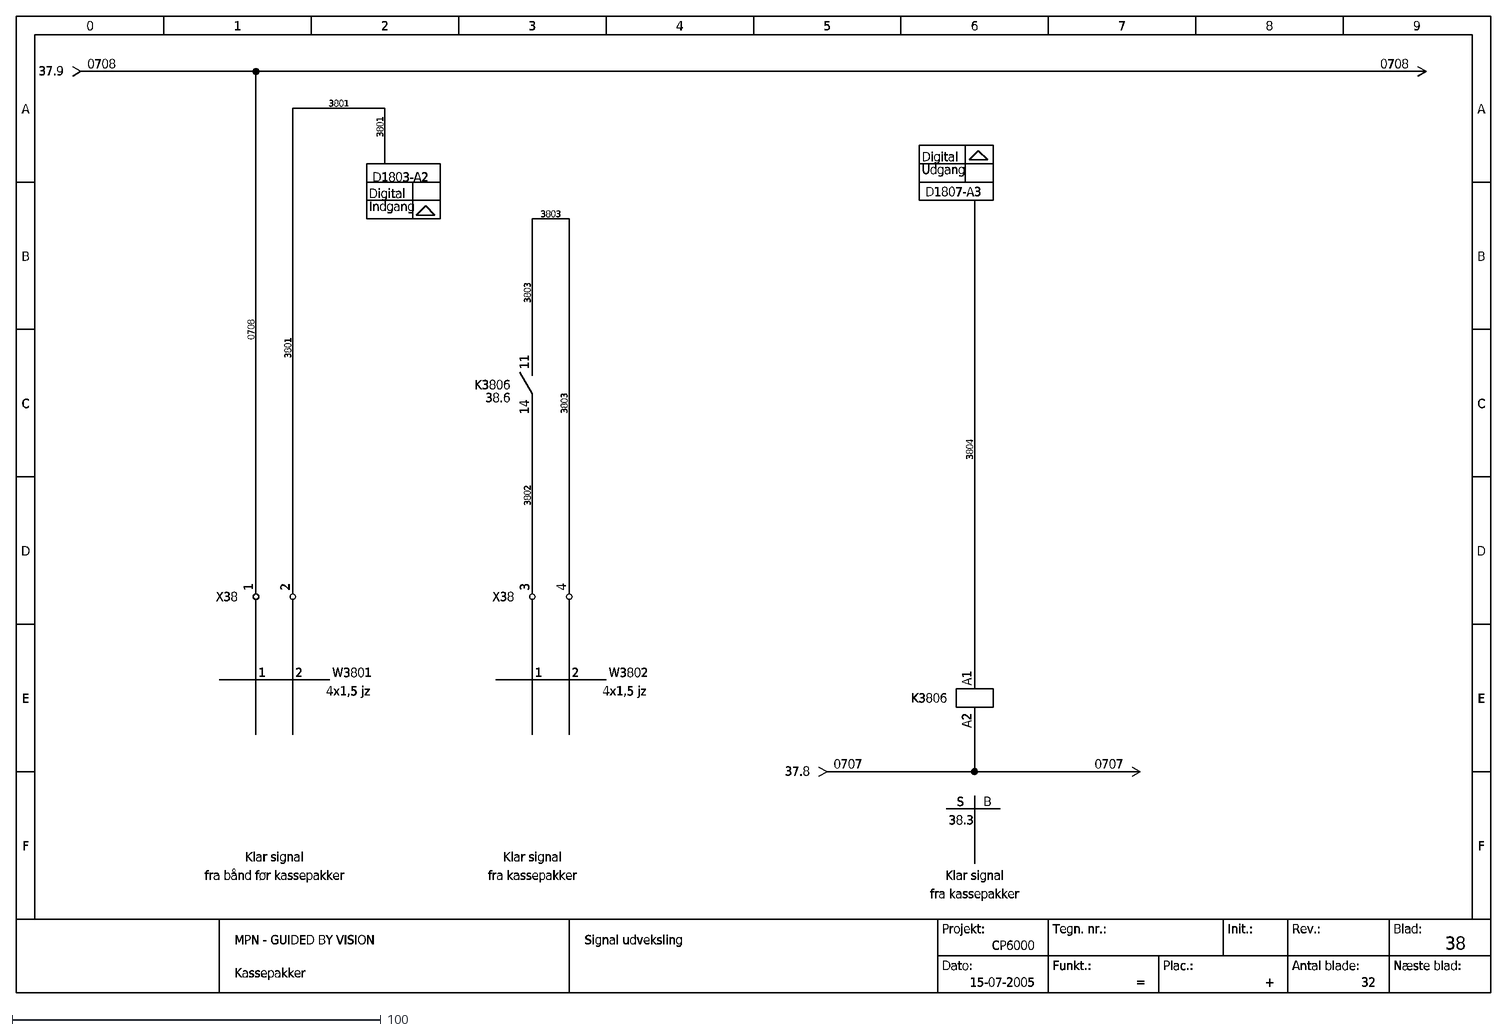
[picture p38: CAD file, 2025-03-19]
cp6000/SignalUdveksling - 0038.dxf
0
1
2
3
4
5
6
7
8
9
A
B
C
D
E
F
Kassepakker
MPN - GUIDED BY VISION
Signal udveksling
Projekt:
Dato:
Funkt.:
Tegn. nr.:
CP6000
15-07-2005
Plac.:
=
+
Rev.:
Init.:
38
Blad:
Næste blad:
Antal blade:
32
0708
37.9
Klar signal
3801
K3806
38.6
11
14
3803
fra kassepakker
fra bånd før kassepakker
W3801
W3802
A1
A2
3804
0707
37.8
4x1,5 jz
D1803-A2
#00000031
Digital
Indgang
D1807-A3
#00000033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

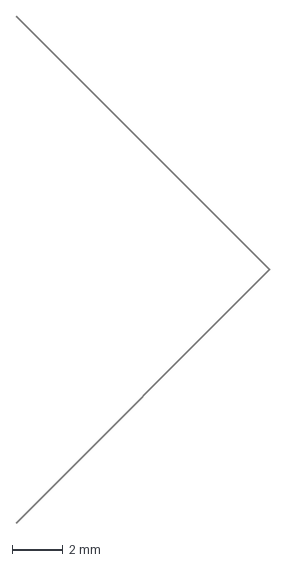
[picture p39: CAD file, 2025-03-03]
CaddyDXF/DFXComponentsLibrary/DigitalComponents/flux_right.dxf
10.0 x 20.0 mm

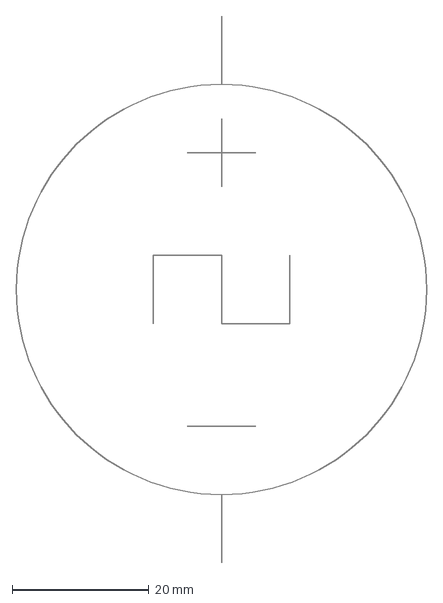
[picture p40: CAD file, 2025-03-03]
CaddyDXF/DFXComponentsLibrary/ElectronicComponents/voltage_source_pulse.dxf
60.0 x 80.0 mm

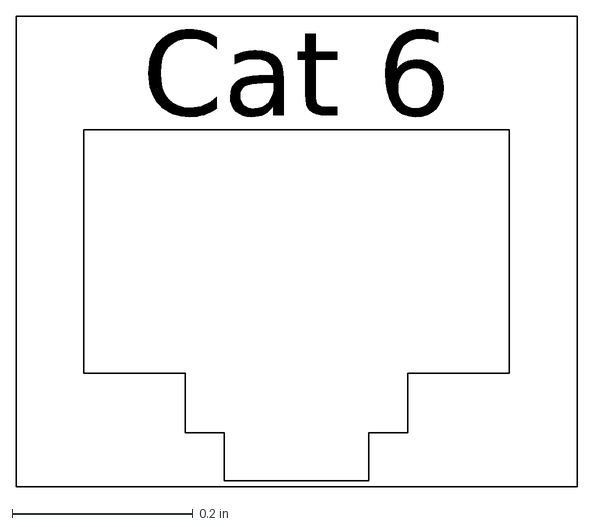
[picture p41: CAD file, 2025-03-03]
CaddyDXF/DFXComponentsLibrary/NetworkComponents/Equipment/Network/RJ45Jack.dxf
Cat 6

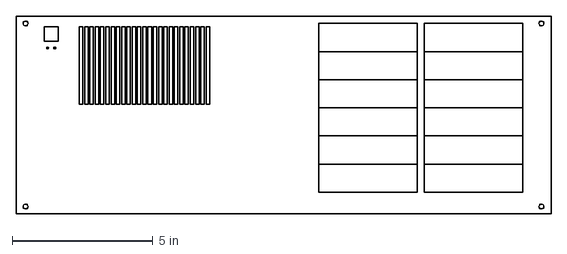
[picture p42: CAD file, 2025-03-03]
CaddyDXF/DFXComponentsLibrary/NetworkComponents/Equipment/Servers/Server4U.dxf
19.0 x 7.00 in

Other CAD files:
CaddyDXF/newDrawings/servoDone/Kassebufferbånd1Done.dxf
CaddyDXF/DFXComponentsLibrary/NetworkComponents/Equipment/Rack/19in21u.dxf
CaddyDXF/DFXComponentsLibrary/NetworkComponents/Logical/Laptop.dxf
CaddyDXF/Kassebufferbånd2 - 0033.dxf
CaddyDXF/DFXComponentsLibrary/DigitalComponents/and.dxf
CaddyDXF/DFXComponentsLibrary/DigitalComponents/flux_left.dxf
CaddyDXF/DFXComponentsLibrary/DigitalComponents/input.dxf
CaddyDXF/DFXComponentsLibrary/DigitalComponents/node.dxf
CaddyDXF/DFXComponentsLibrary/DigitalComponents/not.dxf
CaddyDXF/DFXComponentsLibrary/DigitalComponents/or.dxf
CaddyDXF/DFXComponentsLibrary/ElectronicComponents/amperimeter.dxf
CaddyDXF/DFXComponentsLibrary/ElectronicComponents/bjt_npn.dxf
CaddyDXF/DFXComponentsLibrary/ElectronicComponents/bjt_pnp.dxf
CaddyDXF/DFXComponentsLibrary/ElectronicComponents/capacitor.dxf
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

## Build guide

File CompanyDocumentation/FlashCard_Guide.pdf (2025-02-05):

# FlashCard Guide

Jeppe Fjederholdt Nielsen

September 2020

## Contents

1 Introduction | 1
2 Formatting and imaging | 1
3 Mounting flashcard | 1
4 Replacing database | 1
5 Unmounting the falshcard | 2
6 Touch screen calibration | 2

## 1 Introduction

This Guide will show you how to remove partitions from a flashcard, burn a flashfile onto the flashcard, and set up the database and permissions for the flashcard.

After connecting the flashcard, run ”dmesg” command in terminal. This shows the location of the flashcard e.g. [sdc] 1000944 512-byte logical blocks: (512 MB/489 MiB) . The correct path for the flashcard will be: /dev/sdc. If the flashcard has multiple partitions, you can access it by adding the number of the partition to sdc, so the path of partition 2 would be: /dev/sdc2.

## 2 Formatting and imaging

If the flashcard isn’t empty, start by copying the contents to a flashfile image with this command:

dd if=/dev/sdX of={your location}/flashfil

After this you can format the card with fdisk command:

fdisk /dev/sdX
*** type d ***
*** type the partition number you want to delete ***
*** type d again and repeat ***

Now we want to burn the flashfile image from the github onto the flashcard. This is done by the dd command:

dd if={github location}/flashfil of=/dev/sdX

This operation may take some time.

## 3 Mounting flashcard

Before mounting and editing the flashcards content, make sure you have a folder called /mnt/cf. This should be your mounting point, you will need to mount partition 2:

sudo mount /dev/sdX2 /mnt/cf

Now you can access the contents in the folders /mnt/cf.

## 4 Replacing database

Now you need to replace the database on the flashcard, with the one you work with. Go to the mounting point:

cd /mnt/cf

Remove the previous database from the flashcard:

sudo rm -r database

copy the database you are working with:

sudo cp -r /{location of your database} /mnt/cf

before editing you need to confirm the permissions of the contents in /mnt/cf :

ls -l /mnt/cf

It should look like figure 1. But the ownership of database would be yours.

1

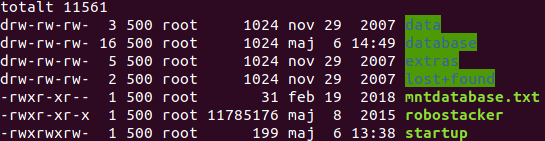
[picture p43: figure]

Figure 1: ls -l of /mnt/cf

Now you have to change the permissions of the database with chown:

sudo chown -R 500:root database

Lastly you need to edit mntdatabase.txt for it to run your system.

## 5 Unmounting the falshcard

For unmounting you have to close all documents related to the card, and change directory in the terminal with cd command. Now use umount to unmount the flashcard:

sudo umount /mnt/cf

Go to your folder manager and eject the flashcard. You can now remove the flashcard.

## 6 Touch screen calibration

For the big panel pc the touch port is touchport=/dev/ttyS2 and ttyS3 for the small. This is changed in the system.ini file in the database. To calibrate the touch screen, the value touch.initialized need to be set to 0.

NOTICE!! If you haven’t changed the touchport value in system.ini then you don’t need to calibrate.

Now when you turn on the panel pc it will start with a calibration screen, unfortunately you have too be a bit fast to calibrate the screen. Just follow the instructions on the screen and it will calibrate.

2

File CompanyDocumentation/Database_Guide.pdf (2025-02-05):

## Beskrivende Indholdsliste til MRN Software

Frederik Hartig, Jeppe Fjederholdt Nielsen

Marts 2020

## 1 Introduktion

Denne dokumentation beskriver hvilke mapper og filer der skal bruges for at få MRN Software til at kører HMI’et. Programmet er opsat af tekstbaseret filer som læses og eksekveres af kode skrevet i C++ der ligger i Sandbox mappen. Den overordenet mappe for et robot system har workcell’ens id [wid] som navn f.eks 350. I mappen skal der være disse mapper og filer:

- mappe: data
- mappe: database
- fil: mntdatabase.txt
- executable: robostacker
- script: [wid].sh (valgfri)
- mappe: extras (Flash Kort)
- script: startup (Flash Kort)
- script: connect2mpn.sh (Flash Kort)

Punkter med (Flash Kort) skal inkluderes på Flash kortet men kan godt undværes hvis robostacker programmet køres fra en pc. HMI’et startes ved at kører den eksekverbare fil robostacker, denne fil skal bruge en mntdatabase.txt fil der indeholder stien til databasen og den gældende workcells system.ini fil. et eksempel på mntdatabase.txt kan ses i table 1

database
[wid]system.ini

Table 1: mntdatabase.txt

1

2 DATA | Section - 2

## 2 data

Her ligger der filer til HMI’et:

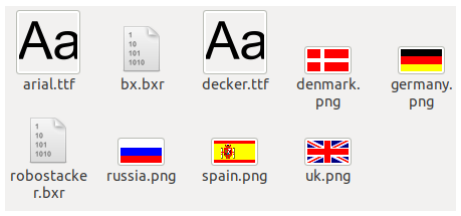
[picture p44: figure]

- font: arial.ttf
- font: decker.ttf
- HMI fil: bx.bxr
- HMI fil: robostacker.bxr
- png: denmark
- png: germany
- png: russia
- png: spain
- png: uk

Da det kun er HMI’et i sig selv der skal bruge disse filer, har de ikke nogen kritisk betydning for programmet. Men data skal stadig være i [wid] mappen.

Side 2 af 5

3 DATABASE | Section - 3

## 3 database

Denne mappe indeholder undermapper med teksttype filer til at styre systemet, listen her viser hvilke mapper databasen skal indeholde:

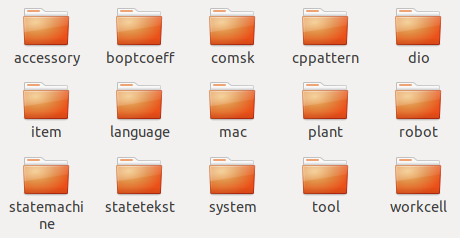
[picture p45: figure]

- boptcoeff
- dio
- item
- language
- plant
- robot
- statemachine
- statetekst
- system
- tool
- workcell
- accessory (mpnguide valgfri)
- comsk (CP6000)
- cppattern (CP6000)
- mac (CP6000)

### 3.1 boptcoeff

[wid].boptcoeff diffinere robottens pathing, ved hjælp af Frames, Items, Pathtype, -mode og via positions. Filen bliver brugt til at snakke med Trio motion coordinator som styre robottens bevægelser. Opsætningen af en boptcoeff path er småt beskrevet i "MPN banefremstilling.pdf", en mere dybdegående guide findes i "DocumentationofBoptcoeff.pdf”.

### 3.2 dio

[wid].io filen er en fil der indeholder alle oplysning på I/O portene. Filen er opdelt i forskellige advantys moduler, med deres connections. Alle de brugte I/O forbindelser bliver givet et navn, det navn kan derved tilkaldes i en statemachine hvor porten, afhængig af om det er en input eller output port, henholdvis kan læses eller skrives til. Der henvises til dokumentet "Diof ile.pdf”foryderligereinformation.

### 3.3 item

[item].item filer indeholder dimensionerne på en kasse eller objekt som robotten kan håndtere. Et item kan være en BOX, BAG eller NET og den har dimensioner og vægt. Item filer bliver brugt i forhold til robot programmet "program.statemachine" og "programB[X].statemachine", for at hole styr på hvilke slags kasse som robotten skal håndtere og hvordan de skal depalleteres og palleteres.

### 3.4 language

[language].language filer indeholder de forskellige sprog HMI’et kan bruge. Det tager udgangspunkt i Dansk som hoved sprog. I filerne er opbygning, et nummer, en oversættelse og den engelske sætning.

Side 3 af 5

### 3.5 plant

[wid].plant filen indeholder hvilken workcell der skal bruges til i systemet. Der kan ikke bruges mere end én workcell per plant.

### 3.6 robot

[wid].robot denne fil har robottens dimensioner og kinamtik samt gearing og Frames. Filen snakker sammen med Trio motion coordinator og programmet på HMI’et.

### 3.7 statemachine

[wid][statemachine].statemachine er en gruppe af filer der indholder statemachines for alle segmenter i systemet, inklusiv robotten. Filerne kan indeholde sensor input og output der bliver brugt til at styre de forskellige states et segment er i. Det er muligt at kigge på en anden statemachines tilstand ved at linke den ønskede statemachine, det er sådan segmenterne snakker sammen.

### 3.8 statetekst

STATETEKST filer indeholder de forskellige fejl og info koder som HMI’et kan vise på skærmen. Deres navn beskriver sproget de er på.

### 3.9 system

[wid]system.ini har instillingerne for programmets HMI, panel pc’en, workcell’en og Trio’en. Den indeholder også user og password til HMI superuser.

### 3.10 tool

[wid].tool filen beskriver lige som ITEM filerne dimensionerne og vægten på det tool robotten har på.

### 3.11 workcell

[wid].workcell er en file der indeholder alle programmets filetyper:

- ITEM
- STATETEKST
- LANGUAGE
- ROBOT
- TOOL
- DIO
- STM
- BOPTCOEFF
- ACCESSORY (mpnguide valgfri)
- COMSK (CP6000)
- CPPATTERN (CP6000)

Side 4 af 5

- MAC (CP6000)

Hvis en statemachine ikke er nævnt i workcell filen kan det være den stadig bliver brugt i andre statemachines ved brug af "include" og er nødvendig for programmet.

### 3.12 accessory

[segment].accessory er filer der holdesaglig bliver brugt til debuging og simulering af programmet, de er derfor ikke nødvendig at have på flash kortet eller til robostacker programmet.

### 3.13 comsk

[wid].comsk er filer der bliver brugt som en konfiguration fil til kassepakkeren. filen syre parameterne for de forskellige comander sk moduler

### 3.14 cppattern

[wid].cppattern er filer der bliver brugt til kassepakkeren. Filerne inderholder de parmeter langbufferskubet skal skubbe med

### 3.15 mac

[wid].mac er filer kassepakkeren bruger til at styrer de forskellige servo motorer

Side 5 af 5

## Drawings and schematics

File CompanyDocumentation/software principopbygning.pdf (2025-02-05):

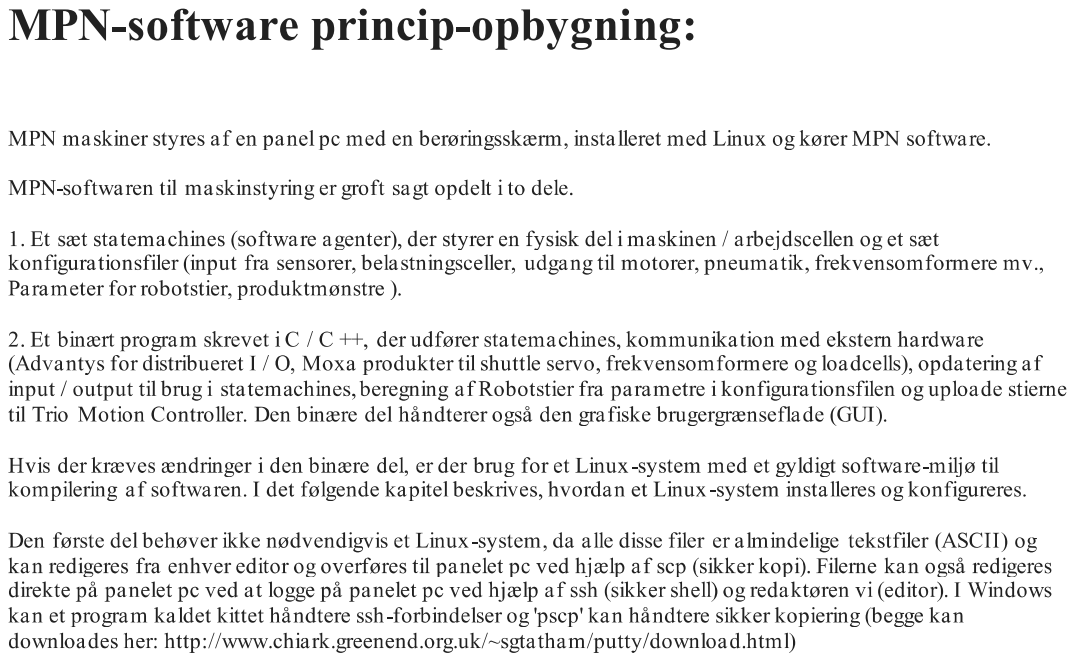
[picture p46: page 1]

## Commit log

2025-03-03 Electronic documentation
    [24VForsyning - 0007.dxf, Advantys - 0013.dxf, Advantys - 0018.dxf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]
2025-03-03 Guide to CAD
    [19in21u.dxf, 19in42u.dxf, 19in9u.dxf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]
2025-03-17 Add files via upload
    CurrentVariables used in vijeo for new HMI
2025-03-19 El documentation
    [Advantys0013Done.dxf, Advantys0014Done.dxf, BufferPladsProxyDone.dxf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]
